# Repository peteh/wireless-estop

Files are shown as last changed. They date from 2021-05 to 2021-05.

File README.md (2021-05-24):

# wireless-estop
**WARNING:** I am not a safety engineer. Therefore the concept that is used and its implementation should not be used in systems that can harm anybody. I take no responsibility for the use or misuse of the system. 

<p align="center">
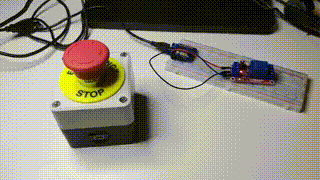
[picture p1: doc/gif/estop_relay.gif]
<br />
Wireless E-Stop connected to relay</p>

This project realizes a wireless E-Stop. It will handle the state of the actual button and also handle connection losses. 

It can be wired to inputs of other systems or directly integrated into Arduino projects that support the ESPNOW! protocol. 

## ESP-NOW! Connection
The Button Station is a Wemos D1 Mini with an attached battery shield and a 1000mAh battery connected to it. Additionally a "Normally Closed" E-Stop button button is wired to the D2 input pin. 

The Base Station is also a Wemos D1 mini that is connected to a relay switch. The state of the E-Stop button is mirrored to the relay switch. 

The state of the button is sent to the master in a given frequency (every 20ms) via the ESP-NOW! protocol. 

There are two causes that can set the system to stopped state. 
 * The button is pressed (E-Stop Button connection is open)
 * The master does not receive a message within a given time frame (timeout)

If the master does not receive a message within a given time it will assume the connection is lost and switch to STOP state. 

## Building the Hardware
### Base Station
The base station is pretty simple and can be set up on a breadboard.
The base station can be pretty much anything. In the example the E-stop button state is mirrored to a relay. It should be wired 'normally closed' and when the E-Stop button is free (not pressed, D2 pin = HIGH) the connection of the relay is closed. 

<p align="center">
<br/>
Schematics: Base station wired to relay
</p>
<p align="center">
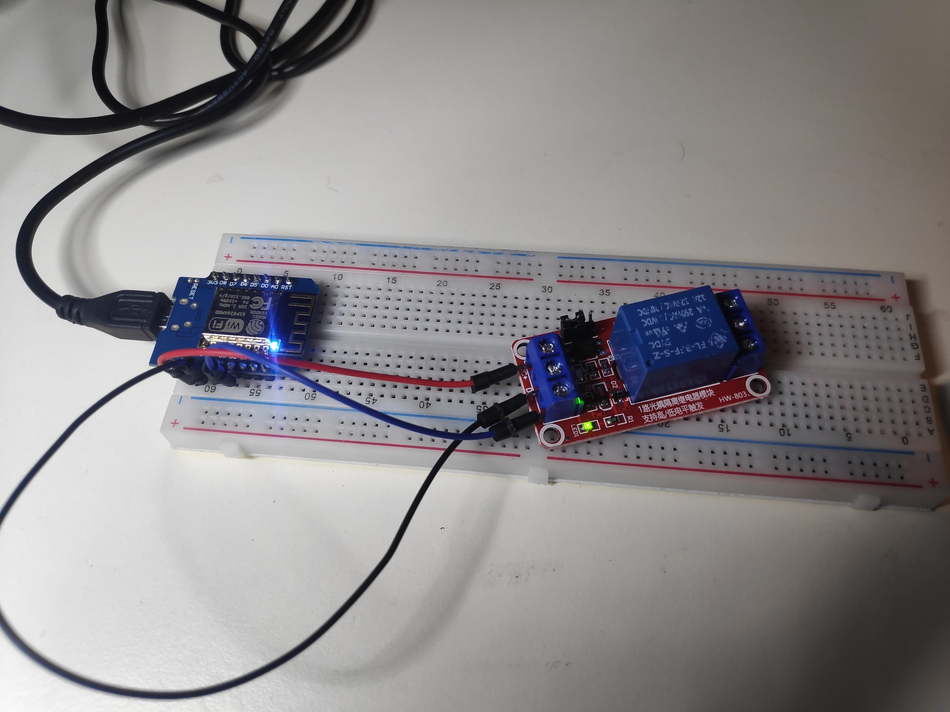
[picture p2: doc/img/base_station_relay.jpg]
<br/>
Base station wired to relay on breadboard</p> 

### E-Stop Button Station
The E-Stop housing was bought as it is and modified by drilling and cutting the necessary holes into it. 

<p align="center">
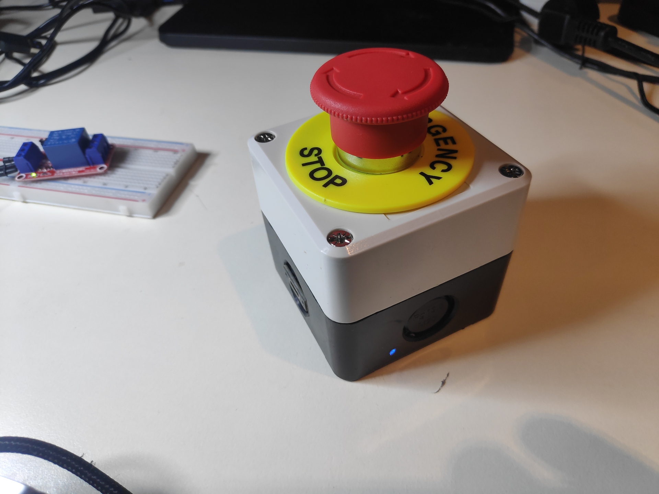
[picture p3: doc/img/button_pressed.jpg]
<br/>
Button pressed with blue LED on the side</p>

<p align="center">
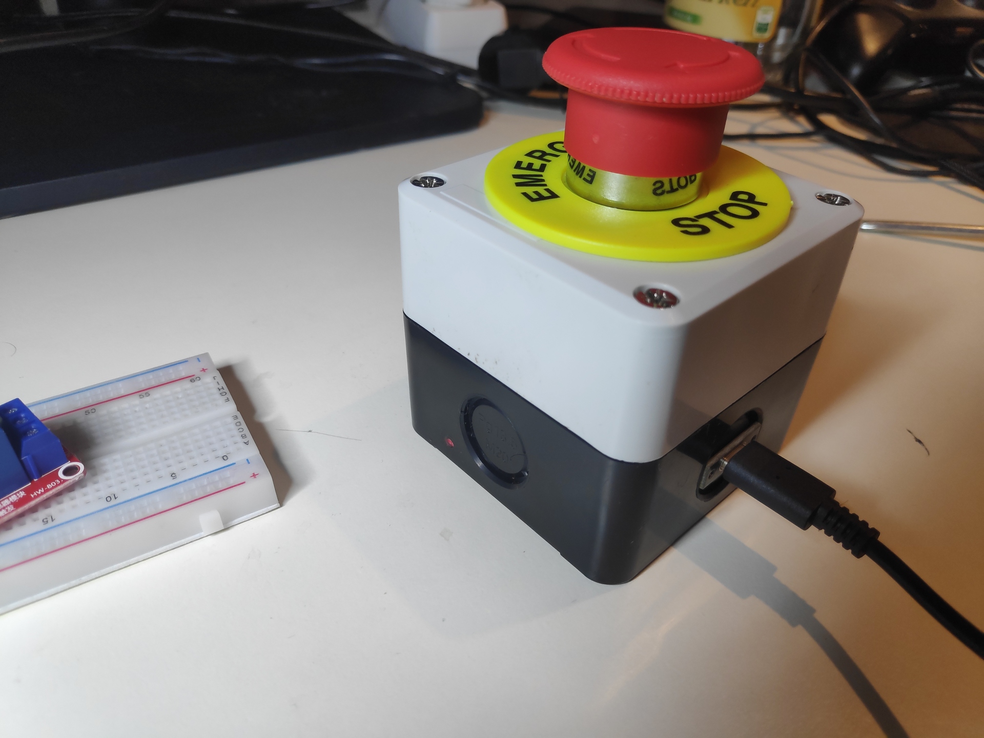
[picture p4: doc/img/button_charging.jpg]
<br/>
Button charging via USB-C with red LED showing charging state</p>

The controller and the power shield have been hot glued to the left and right sides with the onboard LEDs pointing outwards. A hole was drilled into the shell where the LEDs are positioned. Due to hot glueing, the light of the LEDs is forwarded outside, so charging state and controller LED can be seen even if the box is closed. 

Additionally a cable that converts the V+ and GND of the Micro-USB port of the power shield to USB-C has been integrated as well. Thus, the Button can be charged via USB-C chargers. 

<p align="center">
<br/>
Schematics: Button Station</p>

The button station is powered via the Wemos D1 battery shield connected to a 1000mAh lipo battery. It can be turned on or off via the main switch and charged through the battery shield. 

The E-Stop button itself is wired to the D2 pin as an input. 

<p align="center">
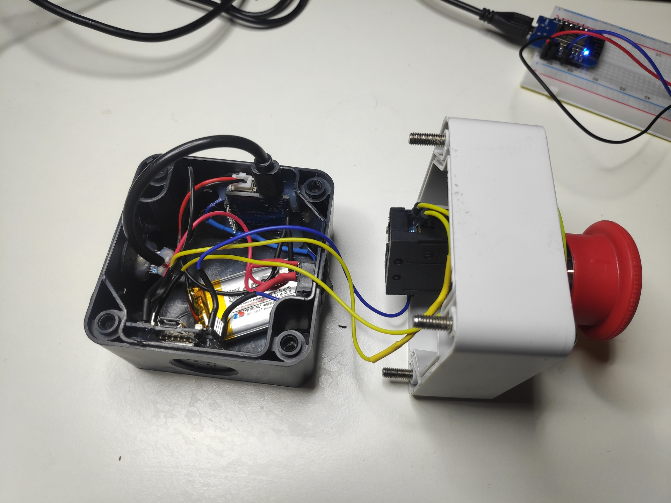
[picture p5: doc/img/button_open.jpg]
<br/>
Inner wiring of the button</p>

## Building the Source
The projects can be built using Visual Studio Code with PlatformIO extension. 
You might have to adapt the upload_port and monitor_port in platformio.ini to match your serial connection. 

To load the project, just add the following folders to your workspace seperately: 
 - libestop (no need to build)
 - estopsrv (build and deploy to base station)
 - estopclient (build and deploy to your button)

### Configuration
In **common/config.h** the system can be configured. The cell id should be adapted to avoid issues with projects compiled in standard configuration.

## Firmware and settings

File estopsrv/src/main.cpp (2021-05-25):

#include <Arduino.h>
#include <ESP8266WiFi.h>
#include <espnow.h>
#include <Log.h>
#include <SerialLogger.h>
#include <EStopReceiver.h>
#include "../../common/config.h"

#define PIN_RELAY D2

estop::EStopReceiver *g_estopReceiver;

void setup()
{
  Log::init(new SerialLogger());

  Serial.begin(115200);
  Serial.println();

  pinMode(LED_BUILTIN, OUTPUT);
  pinMode(PIN_RELAY, OUTPUT);


  // delete old wifi settings
  WiFi.disconnect();

  Log::infof("[OLD] ESP8266 Board MAC Address: %s", WiFi.macAddress().c_str());
  // For Station Mode
  wifi_set_macaddr(STATION_IF, &BASE_STATION_MAC[0]);
  Log::infof("[NEW] ESP8266 Board MAC Address: %s", WiFi.macAddress().c_str());

  WiFi.mode(WIFI_STA); // Place in station mode for ESP-NOW sender node
  //disable sleep mode
  //WiFi.setSleepMode(WIFI_NONE_SLEEP);

  g_estopReceiver = new estop::EStopReceiver(BUTTON_STATION_MAC, WIFI_CHANNEL, CELL_ID, MSG_TIME_MS * SKIP_BEFORE_TIMEOUT);
  g_estopReceiver->init();
}

estop::EStopState g_previousEStopState = estop::ESTOP_ACTIVE;

String eStopStateToStr(estop::EStopState eStopState)
{
  switch (eStopState)
  {
  case estop::ESTOP_ACTIVE:
    return "ESTOP_ACTIVE";
  case estop::ESTOP_FREE:
    return "ESTOP_FREE";
  case estop::ESTOP_TIMEOUT:
    return "ESTOP_TIMEOUT";
  default:
    return "UNDEFINED_TYPE";
  }
}
void loop()
{

  estop::EStopState eStopState = g_estopReceiver->getEStopState();

  if (g_previousEStopState != eStopState)
  {
    Log::infof("EStop State changed: %s -> %s (Battery: %fV)",
               eStopStateToStr(g_previousEStopState).c_str(), 
               eStopStateToStr(eStopState).c_str(), 
               g_estopReceiver->getBatteryVoltage());
  }

  digitalWrite(LED_BUILTIN, eStopState == estop::ESTOP_FREE);
  digitalWrite(PIN_RELAY, eStopState == estop::ESTOP_FREE);
  g_previousEStopState = eStopState;
  // TODO I think we can make this loop event driven and make it sleep more
}

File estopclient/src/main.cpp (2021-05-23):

#include <Arduino.h>
#include <ESP8266WiFi.h>
#include <espnow.h>
#include <Log.h>
#include <SerialLogger.h>

#include "../../common/config.h"
#include <common_types.h>
#include <EStopSender.h>

#define BUTTON_PIN_D2 D2
#define ANALOG_PIN_A0 A0

bool g_previousEStopFree = false;

estop::EStopSender* g_eStopSender;

void setup()
{
  Log::init(new SerialLogger());

  Serial.begin(115200);
  pinMode(LED_BUILTIN, OUTPUT);
  pinMode(BUTTON_PIN_D2, INPUT);
  pinMode(ANALOG_PIN_A0, INPUT);

  delay(10);

    // delete old wifi settings
  WiFi.disconnect();

  // Set device as a Wi-Fi Station
  WiFi.mode(WIFI_STA);
  //WiFi.setSleepMode(WIFI_NONE_SLEEP);

  Log::infof("[OLD] ESP8266 Board MAC Address: %s", WiFi.macAddress().c_str());
  // For Soft Access Point (AP) Mode
  //wifi_set_macaddr(SOFTAP_IF, &newMACAddress[0]);
  // For Station Mode
  wifi_set_macaddr(STATION_IF, &BUTTON_STATION_MAC[0]);
  Log::infof("[NEW] ESP8266 Board MAC Address: %s", WiFi.macAddress().c_str());

  g_eStopSender = new estop::EStopSender(WIFI_CHANNEL, CELL_ID);

  // init communication
  g_eStopSender->init();

  // Register peer
  // TODO: we only use broadcast, no need to add base station as as peer
  //esp_now_add_peer(BASE_STATION_MAC, ESP_NOW_ROLE_SLAVE, WIFI_CHANNEL, NULL, 0);
  
  // init vars to force update
  g_previousEStopFree = !(digitalRead(BUTTON_PIN_D2) > 0);
}

void loop()
{
  bool eStopFree = digitalRead(BUTTON_PIN_D2) > 0;
  float raw = analogRead(A0);
  float voltage = raw / 1023.0 * 4.2;

  digitalWrite(LED_BUILTIN, eStopFree);

  if (eStopFree != g_previousEStopFree)
  {
    Log::infof("Estop free changed %d -> %d", g_previousEStopFree, eStopFree);
    Log::infof("Voltage: %f", voltage);
  }

  // Send message via ESP-NOW
  g_eStopSender->sendState(eStopFree, voltage);
  g_previousEStopFree = eStopFree;

  delay(MSG_TIME_MS);
}

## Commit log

2021-05-14 CHG: extend logger and blink internal led when message received
2021-05-14 CHG: make loop shorter
    [main.cpp]
2021-05-17 ADD: fritinzg schematic
    [remote-estop.fzz]
2021-05-18 ADD: battery voltage
2021-05-19 ADD: final wiring for fritzing
    [remote-estop.fzz]
2021-05-21 CHG: rename file and add switch
    [remote-estop.fzz, wireless-estop.fzz]
2021-05-23 CHG: rename to wireless estop
2021-05-23 CHG: move fritzing to doc folder
    [wireless-estop.fzz]
2021-05-23 CHG: better timeout handling and added fritzing for base
    [wireless-estop-base.fzz, wireless-estop.fzz]
2021-05-23 CHG: rename fritzing
    [wireless-estop-button.fzz]
2021-05-23 CHG: port to esp32 as well (so painful)
